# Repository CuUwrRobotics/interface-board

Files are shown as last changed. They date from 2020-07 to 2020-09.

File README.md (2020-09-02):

# Robot Hardware Interface Board

This repository contains [@nichlock](https://github.com/nichlock)'s design for our hardware interfacing board. This is the board which the [board-interface](https://github.com/CuUwrRobotics/PiranhaBot-docs/blob/master/board_interface/README.md) package is designed to control. 

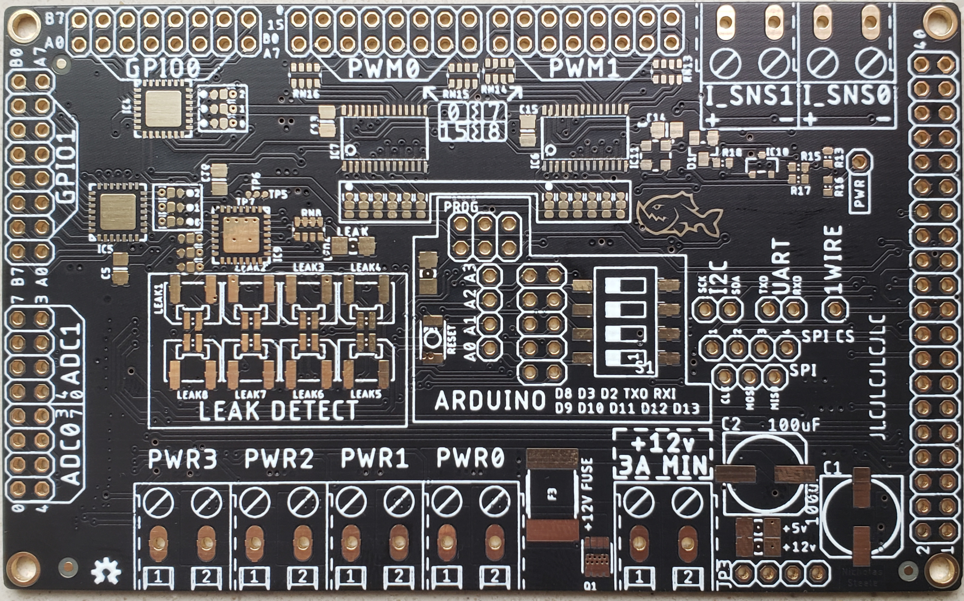
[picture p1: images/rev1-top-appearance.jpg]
Top of board, outside appearence


# Capabilities

This board is designed for our underwater robot, and connects to the Raspebrry Pi through the 40-pin header on the right. It has the following dedicated capabilities:
- 32 GPIO pins
- 32 PWM outputs
- 16 Analog inputs
- 8 Individual leak sensors
- 4 MOSFETs capable of driving 17A (connector limited)
- 2 Current sensors capable of 17A (connector limited, sensors are capable of 50A)
- 1 Microcontroller for I/O that needs constant attention
- 1 Configuration chooser, with 4 switches, for changing any setting on the fly

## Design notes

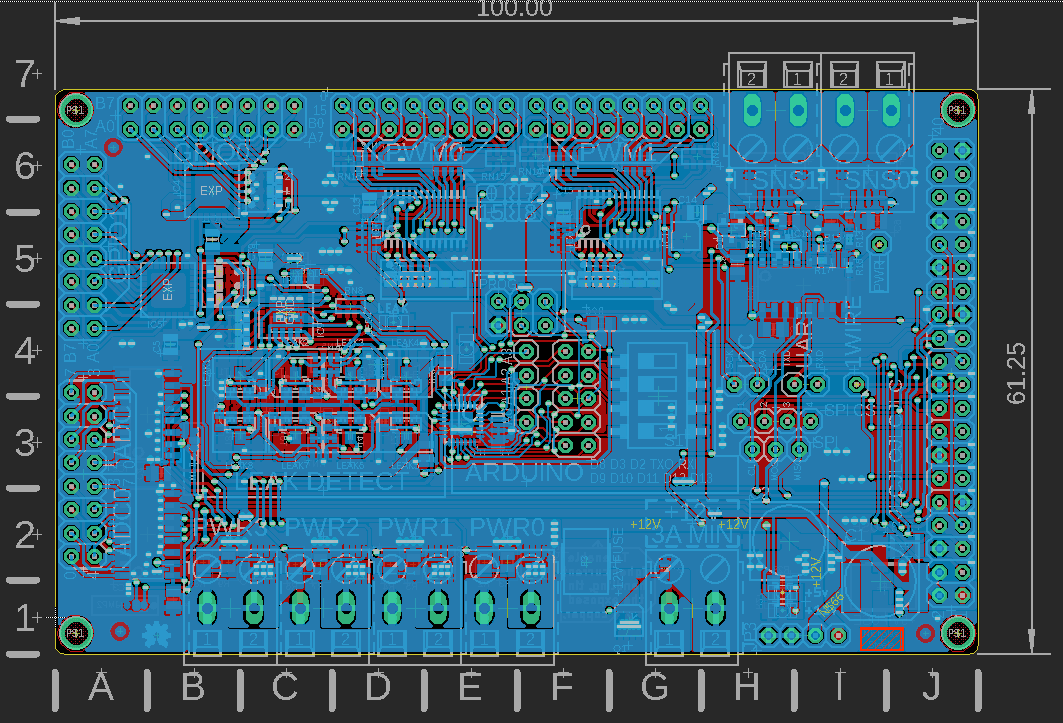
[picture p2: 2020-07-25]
images/rev1-bot-guts.png

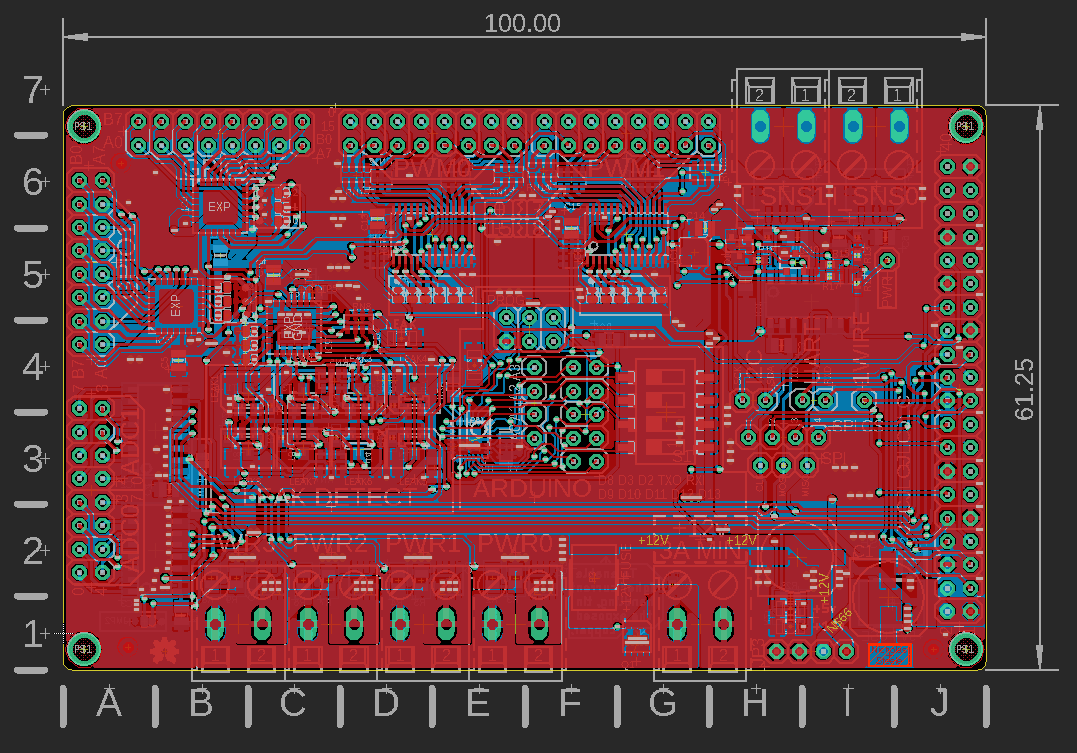
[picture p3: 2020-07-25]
images/rev1-top-guts.png

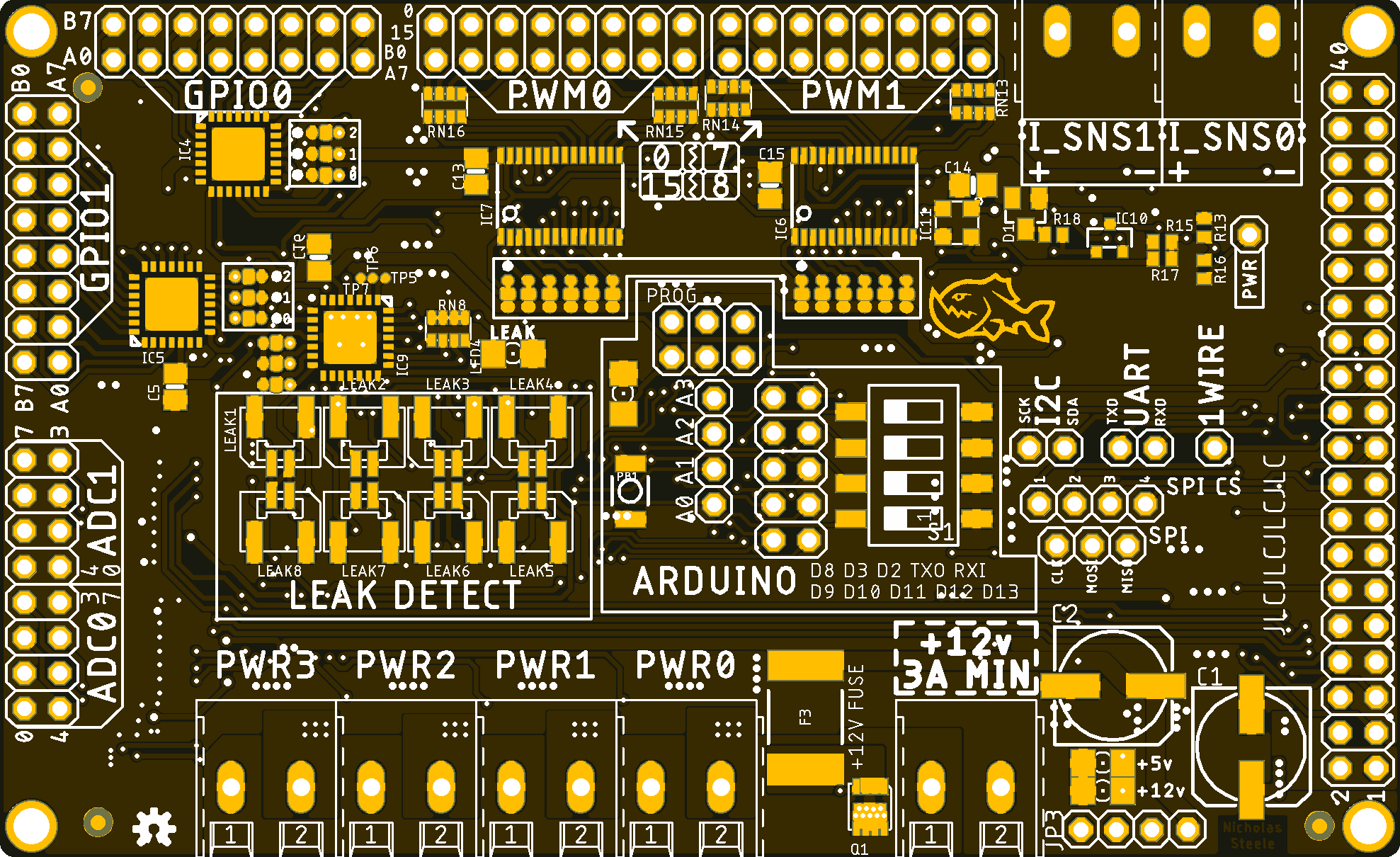
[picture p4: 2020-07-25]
images/rev1-top-appearance.png

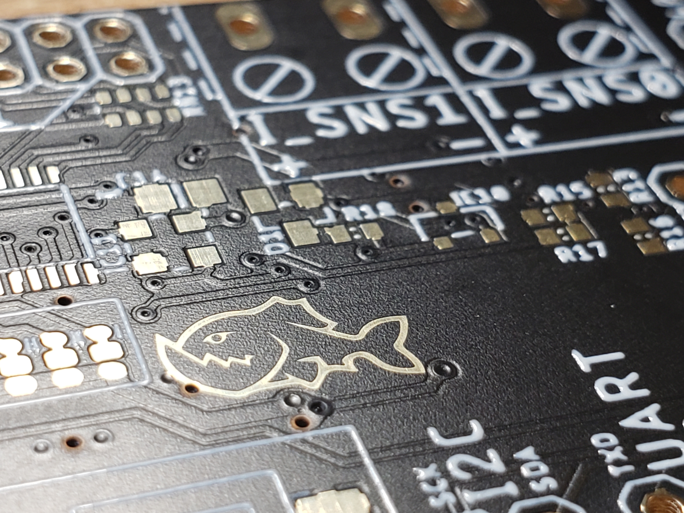
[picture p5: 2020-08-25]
images/piranha.jpg

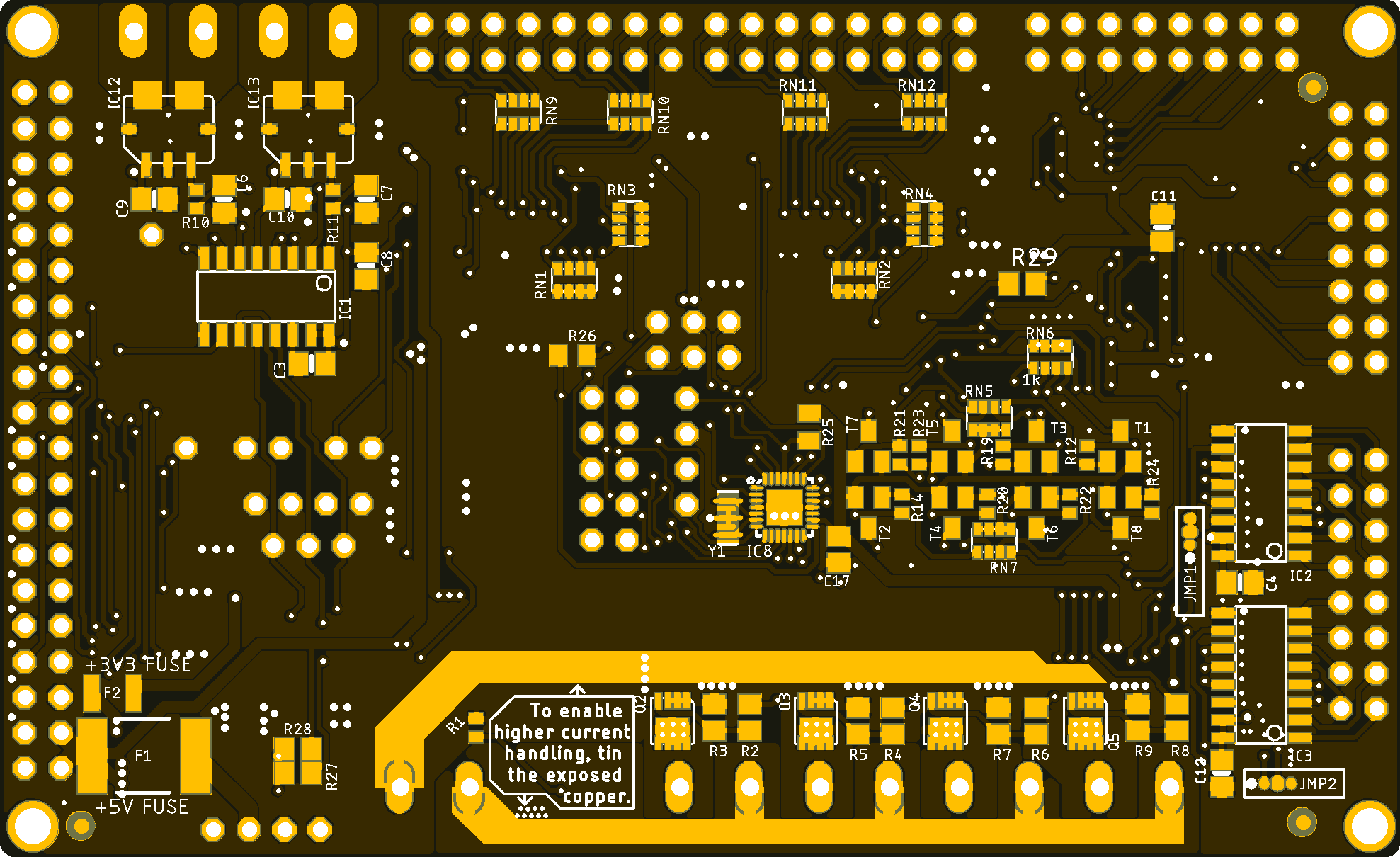
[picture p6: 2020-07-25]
images/rev1-bot-appearance.png

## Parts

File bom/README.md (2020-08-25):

# How to use this BOM

For purchasing, use `Circuit Board BOM.xlsx`. Enter the '1' for the functions you want included in the board on the table to the right, then copy the parts from the Auto Exporter page into Digikey/Mouser's BOM importer tools.

For an interactive BOM, use the files from the `interactive` directory in our web browser.

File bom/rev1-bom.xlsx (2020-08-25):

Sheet: Eagle Parts
100 | Value | Device | Package | Description | MFR ID | Mouser P/N | Digikey P/N | Cost | Count | Feature | Include? (1/0) | Cost Impact | Cost impact calc
C1 | 100uF | CPOL-US153CLV-0807 | 153CLV-0807 | Big 5v cap | PCV1J270MCL7GS | 647-PCV1J270MCL7GS |  | $2.82 | x | REQUIRED | x | 10.95 | $71.48
C2 | 100uF | CPOL-US153CLV-0807 | 153CLV-0807 | Big 12v cap | PCV1J270MCL7GS | 647-PCV1J270MCL7GS |  | $2.82 | x | Temp/pressure sensor | x | $3.87 | $31.28
C3 | 1uF | CAP_CERAMIC0805-NOOUTLINE | 0805-NO | ADC | CC0805ZRY5V7BB105 |  | 311-1457-1-ND | $0.16 | x | Current Sensors | 1 | $13.60 | $40.20
C4 | 1uF | CAP_CERAMIC0805-NOOUTLINE | 0805-NO | ADC | CC0805ZRY5V7BB105 |  | 311-1457-1-ND | $0.16 | x | Power switching | 1 | $10.08
C5 | 1uF | CAP_CERAMIC0805-NOOUTLINE | 0805-NO | ADC | CC0805ZRY5V7BB105 |  | 311-1457-1-ND | $0.16 | x | Arduino | x | $5.01
C6 | 1nF | CAP_CERAMIC0805-NOOUTLINE | 0805-NO | Current | CC0805JRX7R9BB102 |  | 311-4270-1-ND | $0.16 | 1 | Leak | 1 | $7.60
C7 | 1nF | CAP_CERAMIC0805-NOOUTLINE | 0805-NO | Current | CC0805JRX7R9BB103 |  | 311-4270-1-ND | $0.16 | 1 | ADC | x | $7.05
C8 | 1uF | CAP_CERAMIC0805-NOOUTLINE | 0805-NO | Temp | CC0805ZRY5V7BB105 |  | 311-1457-1-ND | $0.16 | x | GPIO | x | $3.40
C9 | .1uF | CAP_CERAMIC0805-NOOUTLINE | 0805-NO | Current | CC0805ZRY5V9BB104 |  | 311-1361-1-ND | $0.11 | 1 | PWM | x | $6.30
C10 | .1uF | CAP_CERAMIC0805-NOOUTLINE | 0805-NO | Current | CC0805ZRY5V9BB104 |  | 311-1361-1-ND | $0.11 | 1 | Parts for Security cam interface | 0 | $3.52
C11 | 10uF | CAP_CERAMIC0805-NOOUTLINE | 0805-NO | PWM | CC0805ZKY5V7BB106 | 603-CC805ZKY5V7BB106 |  | $0.29 | x | Already purchased items marked with x
C12 | 10uF | CAP_CERAMIC0805-NOOUTLINE | 0805-NO | PWM | CC0805ZKY5V7BB106 | 603-CC805ZKY5V7BB106 |  | $0.29 | x
C13 | 10uF | CAP_CERAMIC0805-NOOUTLINE | 0805-NO | GPIO | CC0805ZKY5V7BB106 | 603-CC805ZKY5V7BB106 |  | $0.29 | x
C14 | 1uF | CAP_CERAMIC0805-NOOUTLINE | 0805-NO | PRESS | CC0805ZRY5V7BB105 |  | 311-1457-1-ND | $0.16 | x
C15 | 10uF | CAP_CERAMIC0805-NOOUTLINE | 0805-NO | GPIO | CC0805ZKY5V7BB106 | 603-CC805ZKY5V7BB106 |  | $0.29 | x
C16 | 10uF | CAP_CERAMIC0805-NOOUTLINE | 0805-NO | Leak | CC0805ZKY5V7BB106 | 603-CC805ZKY5V7BB106 |  | $0.29 | 1
C17 | 0.1uF | C-EUC0805 | C0805 | Arduino | CC0805ZRY5V9BB104 |  | 311-1361-1-ND | $0.11 | x
D1 | BZX84B3V0-7-F | ZENER-DIODESOT23 | SOT23 | vref | BZX84B3V0-7-F | 621-BZX84B3V0-7-F |  | $0.17 | x
F1 | 3A | PTC_FUSE3 | 2920_(7351_METRIC) | 5v fuse | MF-LSMF300/24X-2 | 652-MF-LSMF300/24X-2 |  | $0.73 | x
F2 | 0.5A | PTC_FUSE2 | 1210_(3225METRIC) | 3v3 fuse | 0ZCH0050FF2G | 530-0ZCH0050FF2G |  | $0.11 | x
F3 | 3A | PTC_FUSE3 | 2920_(7351_METRIC) | 12v fuse | MF-LSMF300/24X-2 | 652-MF-LSMF300/24X-2 |  | $0.73 | x
IC1 | U2 | MCP3008 | MCP3008 | ADC | MCP3008-I/SL |  | MCP3008-I/SL-ND | $2.19 | x
IC2 | U2 | MCP3008 | MCP3008 | ADC | MCP3008-I/SL |  | MCP3008-I/SL-ND | $2.19 | x
IC3 | U2 | MCP3008 | MCP3008 | ADC | MCP3008-I/SL |  | MCP3008-I/SL-ND | $2.19 | x
IC4 | MCP23017ML | MCP23017ML | QFN28-ML_6X6MM | GPIO | MCP23017T-E/ML |  | MCP23017T-E/MLCT-ND | $1.41 | x
IC5 | MCP23017ML | MCP23017ML | QFN28-ML_6X6MM | GPIO | MCP23017T-E/ML |  | MCP23017T-E/MLCT-ND | $1.41 | x
IC6 | PCA9685 | PCA9685 | TSSOP28 | PWM | PCA9685PW/Q900,118 | 771-PCA9685PW,118 |  | $2.26 | x
IC7 | PCA9685 | PCA9685 | TSSOP28 | PWM | PCA9685PW/Q900,118 | 771-PCA9685PW,118 |  | $2.26 | x
IC8 | ATMEGA328P_VQFNVQFN | ATMEGA328P_VQFNVQFN | VQFN-28 | Arduino | ATMEGA328P-MMHR |  | ATMEGA328P-MMHRCT-ND | $2.17 | x
IC9 | MCP23017ML | MCP23017ML | QFN28-ML_6X6MM | Leak | MCP23017T-E/ML |  | MCP23017T-E/MLCT-ND | $1.41 | 1
IC10 | LM62C | LM62C | SOT23-R | Temp | LM62CIM3/NOPB |  | LM62CIM3/NOPBCT-ND | $1.13 | x
IC11 | MS563702BA03-50 | PRESSURE | MS5637 | PRESS | MS563702BA03-50 | 824-MS563702BA03-50 |  | $2.42 | x
IC12 | ACS780LLRTR-050B-T | ACS781 | ACS781 | Current, 100A | ACS780LLRTR-100U-T |  | 620-1820-1-ND | $5.27 | 1
IC13 | ACS780LLRTR-050B-T | ACS781 | ACS781 | Current, 50A | ACS780LLRTR-050U-T |  | 620-1818-1-ND | $5.27 | 1
LEAK1 | JST-GH-2 | JST-GH-2 | JST-GH | Leak | BM02B-GHS-TBT(LF)(SN)(N) |  | 455-1578-1-ND | $0.43 | 1
LEAK2 | JST-GH-2 | JST-GH-2 | JST-GH | Leak | BM02B-GHS-TBT(LF)(SN)(N) |  | 455-1578-1-ND | $0.43 | 1
LEAK3 | JST-GH-2 | JST-GH-2 | JST-GH | Leak | BM02B-GHS-TBT(LF)(SN)(N) |  | 455-1578-1-ND | $0.43 | 1
LEAK4 | JST-GH-2 | JST-GH-2 | JST-GH | Leak | BM02B-GHS-TBT(LF)(SN)(N) |  | 455-1578-1-ND | $0.43 | 1
LEAK5 | JST-GH-2 | JST-GH-2 | JST-GH | Leak | BM02B-GHS-TBT(LF)(SN)(N) |  | 455-1578-1-ND | $0.43 | 1
LEAK6 | JST-GH-2 | JST-GH-2 | JST-GH | Leak | BM02B-GHS-TBT(LF)(SN)(N) |  | 455-1578-1-ND | $0.43 | 1
LEAK7 | JST-GH-2 | JST-GH-2 | JST-GH | Leak | BM02B-GHS-TBT(LF)(SN)(N) |  | 455-1578-1-ND | $0.43 | 1
LEAK8 | JST-GH-2 | JST-GH-2 | JST-GH | Leak | BM02B-GHS-TBT(LF)(SN)(N) |  | 455-1578-1-ND | $0.43 | 1
LED1 |  | LED_E | LED_1206 | Arduino | LTST-C230KFKT | 859-LTST-C230KFKT |  | $0.30 | x
LED2 |  | LED_E | LED_1206 | 5v led | LTST-C230KFKT | 859-LTST-C230KFKT |  | $0.30 | x
LED3 |  | LED_E | LED_1206 | 12v led | LTST-C230KFKT | 859-LTST-C230KFKT |  | $0.30 | x
LED4 |  | LED_E | LED_1206 | Leak | LTST-C230KFKT | 859-LTST-C230KFKT |  | $0.30 | 1
PB1 | RESET | 0173_IT-1185AP1C-160G-G_T&R | SMD_157SW | Arduino | PTS820 J20M SMTR LFS |  | CKN10505CT-ND | $0.45 | x
Q1 | 1212_PFET | 1212_PFET | POWERPACK_1212-8 | reverse polarity | SI7625DN-T1-GE3 | 781-SI7625DN-T1-GE3 |  | $1.01 | x
Q2 | 1212_NFET | 1212_NFET | POWERPACK_1212-8 | pwr | SIS476DN-T1-GE3 |  | SIS476DN-T1-GE3CT-ND | $1.16 | 1
Q3 | 1212_NFET | 1212_NFET | POWERPACK_1212-8 | pwr | SIS476DN-T1-GE3 |  | SIS476DN-T1-GE3CT-ND | $1.16 | 1
Q4 | 1212_NFET | 1212_NFET | POWERPACK_1212-8 | pwr | SIS476DN-T1-GE3 |  | SIS476DN-T1-GE3CT-ND | $1.16 | 1
Q5 | 1212_NFET | 1212_NFET | POWERPACK_1212-8 | pwr | SIS476DN-T1-GE3 |  | SIS476DN-T1-GE3CT-ND | $1.16 | 1
R1 | 10k | R-US_R0402 | R0402 | reverse polarity | RC0805FR-0710KL |  | 311-10.0KCRCT-ND | $0.10 | x
R2 | 10R | R-US_R0805 | R0805 | pwr |  |  |  | $0.10 | 1
R3 | 10k | R-US_R0805 | R0805 | pwr | RC0805FR-0710KL |  | 311-10.0KCRCT-ND | $0.10 | 1
R4 | 10R | R-US_R0805 | R0805 | pwr |  |  |  | $0.10 | 1
R5 | 10k | R-US_R0805 | R0805 | pwr | RC0805FR-0710KL |  | 311-10.0KCRCT-ND | $0.10 | 1
R6 | 10R | R-US_R0805 | R0805 | pwr |  |  |  | $0.10 | 1
R7 | 10k | R-US_R0805 | R0805 | pwr | RC0805FR-0710KL |  | 311-10.0KCRCT-ND | $0.10 | 1
R8 | 10R | R-US_R0805 | R0805 | pwr |  |  |  | $0.10 | 1
R9 | 10k | R-US_R0805 | R0805 | pwr | RC0805FR-0710KL |  | 311-10.0KCRCT-ND | $0.10 | 1
R10 | 10k | R-US_R0402 | R0402 | Current | RC0805FR-0710KL |  | 311-10.0KCRCT-ND | $0.10 | 1
R11 | 10k | R-US_R0402 | R0402 | Current | RC0805FR-0710KL |  | 311-10.0KCRCT-ND | $0.10 | 1
R12 | 1k | R-US_R0402 | R0402 | Leak | RC0402FR-071KL |  | 311-1.00KLRCT-ND | $0.10 | 1
R13 | 1k | R-US_R0402 | R0402 | power line measure | RC0402FR-071KL |  | 311-1.00KLRCT-ND | $0.10 | x
R14 | 1k | R-US_R0402 | R0402 | Leak | RC0402FR-071KL |  | 311-1.00KLRCT-ND | $0.10 | 1
R15 | 1k | R-US_R0402 | R0402 | power line measure | RC0402FR-071KL |  | 311-1.00KLRCT-ND | $0.10 | x
R16 | 11k | R-US_R0402 | R0402 | power line measure | RC0402FR-0711KL |  | 311-11.0KLRCT-ND | $0.10 | x
R17 | 2.2k | R-US_R0402 | R0402 | power line measure | RC0402FR-072K2L |  | 311-2.20KLRCT-ND | $0.10 | x
R18 | 1k | R-US_R0402 | R0402 | vref | RC0402FR-071KL |  | 311-1.00KLRCT-ND | $0.10 | x
R19 | 1k | R-US_R0402 | R0402 | Leak | RC0402FR-071KL |  | 311-1.00KLRCT-ND | $0.10 | 1
R20 | 1k | R-US_R0402 | R0402 | Leak | RC0402FR-071KL |  | 311-1.00KLRCT-ND | $0.10 | 1
R21 | 1k | R-US_R0402 | R0402 | Leak | RC0402FR-071KL |  | 311-1.00KLRCT-ND | $0.10 | 1
R22 | 1k | R-US_R0402 | R0402 | Leak | RC0402FR-071KL |  | 311-1.00KLRCT-ND | $0.10 | 1
R23 | 1k | R-US_R0402 | R0402 | Leak | RC0402FR-071KL |  | 311-1.00KLRCT-ND | $0.10 | 1
R24 | 1k | R-US_R0402 | R0402 | Leak | RC0402FR-071KL |  | 311-1.00KLRCT-ND | $0.10 | 1
R25 | 10k | R-US_R0805 | R0805 | Arduino | RC0805FR-0710KL |  | 311-10.0KCRCT-ND | $0.10 | x
R26 | 1k | R-US_R0805 | R0805 | Arduino | RC0402FR-071KL |  | 311-1.00KLRCT-ND | $0.10 | x
R27 | 1k | R-US_R0805 | R0805 | 5v led | RC0402FR-071KL |  | 311-1.00KLRCT-ND | $0.10 | x
R28 | 1k | R-US_R0805 | R0805 | 12v led | RC0402FR-071KL |  | 311-1.00KLRCT-ND | $0.10 | x
R29 | 1k | R-US_R0805 | R0805 | Leak | RC0402FR-071KL |  | 311-1.00KLRCT-ND | $0.10 | x
RN1 | 10k | RN4_0804 | 0804_RN | PWM | CAY16-103J4LF |  | CAY16-103J4LFCT-ND | $0.10 | x
RN2 | 10k | RN4_0804 | 0804_RN | PWM | CAY16-103J4LF |  | CAY16-103J4LFCT-ND | $0.10 | x
RN3 | 10k | RN4_0804 | 0804_RN | PWM | CAY16-103J4LF |  | CAY16-103J4LFCT-ND | $0.10 | x
RN4 | 10k | RN4_0804 | 0804_RN | PWM | CAY16-103J4LF |  | CAY16-103J4LFCT-ND | $0.10 | x
RN5 | 27k | RN4_0804 | 0804_RN | Leak | CAY16-273J4LF | 652-CAY16-273J4LF |  | $0.10 | 1
RN6 | 1k | RN4_0804 | 0804_RN | Leak | CAY16-102J4LF |  | CAY16-102J4LFCT-ND | $0.10 | 1
RN7 | 27k | RN4_0804 | 0804_RN | Leak | CAY16-273J4LF | 652-CAY16-273J4LF |  | $0.10 | 1
RN8 | 1k | RN4_0804 | 0804_RN | Leak | CAY16-102J4LF |  | CAY16-102J4LFCT-ND | $0.10 | 1
RN9 | 220R | RN4_0804 | 0804_RN | PWM | CAY16-221J4LF |  | CAY16-221J4LFCT-ND | $0.10 | x
RN10 | 220R | RN4_0804 | 0804_RN | PWM | CAY16-221J4LF |  | CAY16-221J4LFCT-ND | $0.10 | x
RN11 | 220R | RN4_0804 | 0804_RN | PWM | CAY16-221J4LF |  | CAY16-221J4LFCT-ND | $0.10 | x
RN12 | 220R | RN4_0804 | 0804_RN | PWM | CAY16-221J4LF |  | CAY16-221J4LFCT-ND | $0.10 | x
RN13 | 220R | RN4_0804 | 0804_RN | PWM | CAY16-221J4LF |  | CAY16-221J4LFCT-ND | $0.10 | x
RN14 | 220R | RN4_0804 | 0804_RN | PWM | CAY16-221J4LF |  | CAY16-221J4LFCT-ND | $0.10 | x
RN15 | 220R | RN4_0804 | 0804_RN | PWM | CAY16-221J4LF |  | CAY16-221J4LFCT-ND | $0.10 | x
RN16 | 220R | RN4_0804 | 0804_RN | PWM | CAY16-221J4LF |  | CAY16-221J4LFCT-ND | $0.10 | x
S1 | SWS004 | SWS004 | SMS-004 | Arduino | A6S-4104-H | 653-A6S-4104-H |  | $1.49 | x
T1 | MMBT3906 | BC807-40-PNP-SOT23-BEC | SOT23-BEC | Leak | MMBT3906-7-F |  | MMBT3906-FDICT-ND | $0.12 | 1
T2 |  | BC807-40-PNP-SOT23-BEC | SOT23-BEC | Leak | MMBT3906-7-F |  | MMBT3906-FDICT-ND | $0.12 | 1
T3 |  | BC807-40-PNP-SOT23-BEC | SOT23-BEC | Leak | MMBT3906-7-F |  | MMBT3906-FDICT-ND | $0.12 | 1
T4 |  | BC807-40-PNP-SOT23-BEC | SOT23-BEC | Leak | MMBT3906-7-F |  | MMBT3906-FDICT-ND | $0.12 | 1
T5 |  | BC807-40-PNP-SOT23-BEC | SOT23-BEC | Leak | MMBT3906-7-F |  | MMBT3906-FDICT-ND | $0.12 | 1
T6 |  | BC807-40-PNP-SOT23-BEC | SOT23-BEC | Leak | MMBT3906-7-F |  | MMBT3906-FDICT-ND | $0.12 | 1
T7 |  | BC807-40-PNP-SOT23-BEC | SOT23-BEC | Leak | MMBT3906-7-F |  | MMBT3906-FDICT-ND | $0.12 | 1
T8 |  | BC807-40-PNP-SOT23-BEC | SOT23-BEC | Leak | MMBT3906-7-F |  | MMBT3906-FDICT-ND | $0.12 | 1
X1 |  | W237-102 | W237-102 | power input | 796689-2 | 571-796689-2 |  | $1.16 | x
X2 |  | W237-102 | W237-102 | pwr | 796689-2 | 571-796689-2 |  | $1.16 | 1
X3 |  | W237-102 | W237-102 | pwr | 796689-2 | 571-796689-2 |  | $1.16 | 1
X4 |  | W237-102 | W237-102 | pwr | 796689-2 | 571-796689-2 |  | $1.16 | 1
X5 |  | W237-102 | W237-102 | pwr | 796689-2 | 571-796689-2 |  | $1.16 | 1
X6 |  | W237-102 | W237-102 | Current | 796689-2 | 571-796689-2 |  | $1.16 | 1
X7 |  | W237-102 | W237-102 | Current | 796689-2 | 571-796689-2 |  | $1.16 | 1
Y1 | 8/16/20MHz | RESONATOR1:1 | RESONATOR-SMD-1:1 | Arduino | CSTNE16M0V530000R0 |  | 490-17948-1-ND | $0.29 | x
 |  |  |  | Cost without count: | $67.96 |  |  | $31.28 | 47
 |  |  |  | Security cam thing |  |  | MAX485CPA+-ND | 3.22 | 0
 |  |  |  | Security cam thing |  |  | 20QBK-ND | 0.1 | 0
 |  |  |  | Security cam thing |  |  | 20QBK-ND | 0.1 | 0
 |  |  |  | Security cam thing |  |  | 10KQBK-ND | 0.1 | 0
 |  |  |  |  | Total for sec. cam |  |  | 0
 |  |  |  | Cost without count: | $71.48 |  |  | $31.28

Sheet: Auto Exporter
Digikey P/N | Total QTY | Cost | Mouser P/N | Total QTY | Cost
0 | 0 | $0.00 | 647-PCV1J270MCL7GS | 0 | $5.64
311-1457-1-ND | 0 | $0.80 | 0 | 0 | $0.00
311-4270-1-ND | 2 | $0.32 | 603-CC805ZKY5V7BB106 | 1 | $1.45
311-1361-1-ND | 2 | $0.33 | 621-BZX84B3V0-7-F | 0 | $0.17
MCP3008-I/SL-ND | 0 | $6.57 | 652-MF-LSMF300/24X-2 | 0 | $1.46
MCP23017T-E/MLCT-ND | 1 | $4.23 | 530-0ZCH0050FF2G | 0 | $0.11
ATMEGA328P-MMHRCT-ND | 0 | $2.17 | 771-PCA9685PW,118 | 0 | $4.52
LM62CIM3/NOPBCT-ND | 0 | $1.13 | 824-MS563702BA03-50 | 0 | $2.42
620-1820-1-ND | 1 | $5.27 | 859-LTST-C230KFKT | 1 | $1.20
620-1818-1-ND | 1 | $5.27 | 781-SI7625DN-T1-GE3 | 0 | $1.01
455-1578-1-ND | 8 | $3.44 | 652-CAY16-273J4LF | 2 | $0.20
CKN10505CT-ND | 0 | $0.45 | 653-A6S-4104-H | 0 | $1.49
SIS476DN-T1-GE3CT-ND | 4 | $4.64 | 571-796689-2 | 6 | $8.12
311-10.0KCRCT-ND | 6 | $0.80 |  | 0 | $0.00
311-1.00KLRCT-ND | 8 | $1.50 |  | 0 | $0.00
311-11.0KLRCT-ND | 0 | $0.10 |  | 0 | $0.00
311-2.20KLRCT-ND | 0 | $0.10 |  | 0 | $0.00
CAY16-103J4LFCT-ND | 0 | $0.40 |  | 0 | $0.00
CAY16-102J4LFCT-ND | 2 | $0.20 |  | 0 | $0.00
CAY16-221J4LFCT-ND | 0 | $0.80 |  | 0 | $0.00
MMBT3906-FDICT-ND | 8 | $0.96 |  | 0 | $0.00
490-17948-1-ND | 0 | $0.29 |  | 0 | $0.00
MAX485CPA+-ND | 0 | $3.22 |  | 0 | $0.00
20QBK-ND | 0 | $0.20 |  | 0 | $0.00
10KQBK-ND | 0 | $0.10 |  | 0 | $0.00
 | 0 | $0.00 |  | 0 | $0.00
 | 0 | $0.00 |  | 0 | $0.00
 | 0 | $0.00 |  | 0 | $0.00
 | 0 | $0.00 |  | 0 | $0.00
 | 43 | $26.96 |  | 10 | $10.97
Overall total |  |  |  |  |  | $37.93

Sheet: Eagle Direct Export
Part | Value | Device | Package | Description | MFR ID | Mouser P/N | Digikey P/N | Cost | Notes | Count | Feature | Include? (1/0) | Cost impact | Cost impact calc | Options description | Cost @ 5 pcbs |  | Mouser | Digikey
C1 | 1uF | C-EUC0805 | C0805 | Ceramic Capacitors | CC0805ZRY5V7BB105 |  | 311-1457-1-ND | $0.16 |  | 1 | Temp sensor | 0 | $1.29 | 63.03 | DHL shipping (4 days) | $17.70 | Total | 18.67 | 19.78
C2 | 10uF | C-EUC0805 | C0805 | Ceramic Capacitors | CC0805ZKY5V7BB106 | 603-CC805ZKY5V7BB106 |  | $0.29 |  | 1 | Current Sensors | 0 | $13.60 | $35.48 | PostLink Shipping (20 days) | $5.34 | Shipping | 7.99 | 5.99
C3 | 100uF | CPOL-US153CLV-0807 | 153CLV-0807 | POLARIZED CAPACITOR, American symbol | PCV1J270MCL7GS | 647-PCV1J270MCL7GS |  | $2.82 | Main decoupling cap for 12v line | 1 | Pressure sesnor | 0 | $2.58 | $27.55
C4 | 10uF | C-EUC0805 | C0805 | Ceramic Capacitors | CC0805ZKY5V7BB106 | 603-CC805ZKY5V7BB106 |  | $0.29 |  | 1 | Power switching | 0 | $10.08 |  | Stencil cost | $7.00 | OVERALL TOTAL | $79.68
C5 | 1uF | C-EUC0805 | C0805 | Ceramic Capacitors | CC0805ZRY5V7BB105 |  | 311-1457-1-ND | $0.16 |  | 1 | Arduino | 1 | $4.82
C6 | 10uF | C-EUC0805 | C0805 | Ceramic Capacitors | CC0805ZKY5V7BB106 | 603-CC805ZKY5V7BB106 |  | $0.29 |  | 1 | OLED | 1 | $2.37 |  | Standard: green, leaded HASL | $2.00
C7 | 10uF | C-EUC0805 | C0805 | Ceramic Capacitors | CC0805ZKY5V7BB106 | 603-CC805ZKY5V7BB106 |  | $0.29 |  | 1 |  |  |  |  | Remove order number | $1.50
C7 | 10uF | C-EUC0805 | C0805 | Ceramic Capacitors | CC0805ZKY5V7BB106 | 603-CC805ZKY5V7BB106 |  | $0.29 |  | 1 |  |  |  |  | Black soldermask | $0.00
C8 | 1uF | C-EUC0805 | C0805 | Ceramic Capacitors | CC0805ZRY5V7BB105 |  | 311-1457-1-ND | $0.16 |  | 1 |  |  |  |  | Lead-free HASL | $5.30
C9 | 1uF | C-EUC0805 | C0805 | Ceramic Capacitors | CC0805ZRY5V7BB105 |  | 311-1457-1-ND | $0.16 |  | 1 |  |  |  |  | ENIG plating | $16.00
C10 | 1uF | C-EUC0805 | C0805 | Ceramic Capacitors | CC0805ZRY5V7BB105 |  | 311-1457-1-ND | $0.16 |  | 1
C11 | 1uF | C-EUC0805 | C0805 | Ceramic Capacitors | CC0805ZRY5V7BB105 |  | 311-1457-1-ND | $0.16 |  | 1
C12 | 10uF | C-EUC0805 | C0805 | Ceramic Capacitors | CC0805ZKY5V7BB106 | 603-CC805ZKY5V7BB106 |  | $0.29 |  | 1
C13 | 2.2uF | C-EUC0805 | C0805 | Ceramic Capacitors | CC0805ZRY5V7BB225 |  | 311-1463-1-ND | $0.19 |  | 1
C14 | 1uF | C-EUC0805 | C0805 | Ceramic Capacitors | CC0805ZRY5V7BB105 |  | 311-1457-1-ND | $0.16 |  | 0
C15 | .1uF | C-EUC0805 | C0805 | Ceramic Capacitors | CC0805ZRY5V9BB104 |  | 311-1361-1-ND | $0.11 |  | 0
C16 | 1uF | C-EUC0805 | C0805 | Ceramic Capacitors | CC0805ZRY5V7BB105 |  | 311-1457-1-ND | $0.16 |  | 0
C17 | .1uF | C-EUC0805 | C0805 | Ceramic Capacitors | CC0805ZRY5V9BB104 |  | 311-1361-1-ND | $0.11 |  | 0
C18 | 1uF | C-EUC0805 | C0805 | Ceramic Capacitors | CC0805ZRY5V7BB105 |  | 311-1457-1-ND | $0.16 |  | 1
C19 | 1uF | C-EUC0805 | C0805 | Ceramic Capacitors | CC0805ZRY5V7BB105 |  | 311-1457-1-ND | $0.16 |  | 0
C20 | 1uF | C-EUC0805 | C0805 | Ceramic Capacitors | CC0805ZRY5V7BB105 |  | 311-1457-1-ND | $0.16 |  | 0
C22 | 100uF | CPOL-US153CLV-0807 | 153CLV-0807 | POLARIZED CAPACITOR, American symbol | PCV1J270MCL7GS | 647-PCV1J270MCL7GS |  | $2.82 | Main decoupling cap for 5v line | 1
C23 | 0.1uF | C-EUC0805 | C0805 | Ceramic Capacitors | CC0805ZRY5V9BB104 |  | 311-1361-1-ND | $0.11 |  | 1
C24 | 0.1uF | C-EUC0805 | C0805 | Ceramic Capacitors | CC0805ZRY5V9BB104 |  | 311-1361-1-ND | $0.11 |  | 1
D1 | 1N4148 | DIODESOD-323 | SOD-323 | Diode | 1N4148WS-7-F |  | 1N4148WS-FDICT-ND | $0.17 |  | 1
D2 | BZX84B3V0-7-F | ZENER-DIODESOT23 | SOT23 | Z-Diode | BZX84B3V0-7-F | 621-BZX84B3V0-7-F |  | $0.17 |  | 1
F1 | 3A | PTC_FUSE3 | 2920_(7351_METRIC) |  | MF-LSMF300/24X-2 | 652-MF-LSMF300/24X-2 |  | $0.73 | 12V fuse | 1
F2 | 3A | PTC_FUSE | 2920_(7351_METRIC) | Bel Fuse Inc. | MF-LSMF300/24X-2 | 652-MF-LSMF300/24X-2 |  | $0.73 | 5V fuse | 1
F3 | .5A | PTC_FUSE | 1210_(3225METRIC) | Bel Fuse Inc. | 0ZCH0050FF2G | 530-0ZCH0050FF2G |  | $0.11 | 3V3 fuse | 1
IC1 | MCP23017ML | MCP23017ML | QFN28-ML_6X6MM |  | MCP23017T-E/ML |  | MCP23017T-E/MLCT-ND | $1.41 | GPIO Expander | 1
IC2 | MCP23017ML | MCP23017ML | QFN28-ML_6X6MM |  | MCP23017T-E/ML |  | MCP23017T-E/MLCT-ND | $1.41 | GPIO Expander | 1
IC3 | U2 | MCP3008 | MCP3008 |  | MCP3008-I/SL |  | MCP3008-I/SL-ND | $2.19 | ADC | 1
IC4 | U2 | MCP3008 | MCP3008 |  | MCP3008-I/SL |  | MCP3008-I/SL-ND | $2.19 | ADC | 1
IC5 | U2 | MCP3008 | MCP3008 |  | MCP3008-I/SL |  | MCP3008-I/SL-ND | $2.19 | ADC | 1
IC7 | PCA9685 | PCA9685 | TSSOP28 | PCA9685 - 16 Channel 12-Bit I2C PWM Controller | PCA9685PW/Q900,118 | 771-PCA9685PW,118 |  | $2.26 | PWM Driver | 1
IC8 | PCA9685 | PCA9685 | TSSOP28 | PCA9685 - 16 Channel 12-Bit I2C PWM Controller | PCA9685PW/Q900,118 | 771-PCA9685PW,118 |  | $2.26 | PWM Driver | 1
IC9 | MS563702BA03-50 | PRESSURE | MS5637 | Pressure Sensor | MS563702BA03-50 | 824-MS563702BA03-50 |  | $2.42 | Ambient Pressure | 0
IC10 | ACS780LLRTR-050B-T | ACS781 | ACS781 |  | ACS780LLRTR-050B-T |  | 620-1817-1-ND | $5.27 | Current sensor | 0
IC11 | ACS780LLRTR-050B-T | ACS781 | ACS781 |  | ACS780LLRTR-050B-T |  | 620-1817-1-ND | $5.27 | Current sensor | 0
IC12 | LM62C | LM62C | SOT23-R | TI's Thermal Sensor LM62CIM3/NOPB | LM62CIM3/NOPB |  | 926-LM62CIM3/NOPB | $1.13 | Ambient temp sensor | 0
IC13 | ATMEGA328P_VQFNVQFN | ATMEGA328P_VQFNVQFN | VQFN-28 | Atmel 328P | ATMEGA328P-MMHR |  | ATMEGA328P-MMHRCT-ND | $2.17 | Arduino chip | 1
LED1 |  | LED_E | LED_1206 | LED | LTST-C230KFKT | 859-LTST-C230KFKT |  | $0.30 |  | 1
LED2 |  | LED_E | LED_1206 | LED | LTST-C230KFKT | 859-LTST-C230KFKT |  | $0.30 |  | 1
LED3 |  | LED_E | LED_1206 | LED | LTST-C230KFKT | 859-LTST-C230KFKT |  | $0.30 |  | 1
Q1 | 1212_PFET | 1212_PFET | POWERPACK_1212-8 | Vishay Siliconix | SI7625DN-T1-GE3 | 781-SI7625DN-T1-GE3 |  | $1.01 | Reverse voltage protection | 1
Q2 | 1212_NFET | 1212_NFET | POWERPACK_1212-8 | Vishay Siliconix | SIS476DN-T1-GE3 |  | SIS476DN-T1-GE3CT-ND | $1.16 | PWR control fet | 0
Q3 | 1212_NFET | 1212_NFET | POWERPACK_1212-8 | Vishay Siliconix | SIS476DN-T1-GE3 |  | SIS476DN-T1-GE3CT-ND | $1.16 | PWR control fet | 0
Q4 | 1212_NFET | 1212_NFET | POWERPACK_1212-8 | Vishay Siliconix | SIS476DN-T1-GE3 |  | SIS476DN-T1-GE3CT-ND | $1.16 | PWR control fet | 0
Q5 | 1212_NFET | 1212_NFET | POWERPACK_1212-8 | Vishay Siliconix | SIS476DN-T1-GE3 |  | SIS476DN-T1-GE3CT-ND | $1.16 | PWR control fet | 0
Q6 | BSS138 | MOSFET-NWIDE | SOT23-WIDE | N-Channel Mosfet | BSS138 | 621-BSS138-13-F |  | $0.24 |  | 1
Q7 | BSS138 | MOSFET-NWIDE | SOT23-WIDE | N-Channel Mosfet | BSS138 | 621-BSS138-13-F |  | $0.24 |  | 1
Q8 | 8/16/20MHz | RESONATOR1:1 | RESONATOR-SMD-1:1 | Resonator | CSTNE16M0V530000R0 |  | 490-17948-1-ND | $0.29 |  | 1
R1 | 10k | R-US_R0805 | R0805 | RESISTOR, American symbol | RC0805FR-0710KL |  | 311-10.0KCRCT-ND | $0.10 |  | 0
R2 | 10k | R-US_R0805 | R0805 | RESISTOR, American symbol | RC0805FR-0710KL |  | 311-10.0KCRCT-ND | $0.10 |  | 0
R3 | 1k | R-US_R0805 | R0805 | RESISTOR, American symbol | RC0805JR-07470RL |  | 311-470ARCT-ND | $0.10 |  | 1
R5 | 1k | R-US_R0805 | R0805 | RESISTOR, American symbol | RC0805JR-07470RL |  | 311-470ARCT-ND | $0.10 |  | 1
R6 | 10k | R-US_R0805 | R0805 | RESISTOR, American symbol | RC0805FR-0710KL |  | 311-10.0KCRCT-ND | $0.10 |  | 0
R7 | 10k | R-US_R0805 | R0805 | RESISTOR, American symbol | RC0805FR-0710KL |  | 311-10.0KCRCT-ND | $0.10 |  | 0
R8 | 10k | R-US_R0805 | R0805 | RESISTOR, American symbol | RC0805FR-0710KL |  | 311-10.0KCRCT-ND | $0.10 |  | 0
R9 | 10k | R-US_R0805 | R0805 | RESISTOR, American symbol | RC0805FR-0710KL |  | 311-10.0KCRCT-ND | $0.10 |  | 0
R10 | 10k | R-US_R0805 | R0805 | RESISTOR, American symbol | RC0805FR-0710KL |  | 311-10.0KCRCT-ND | $0.10 |  | 0
R11 | 10k | R-US_R0805 | R0805 | RESISTOR, American symbol | RC0805FR-0710KL |  | 311-10.0KCRCT-ND | $0.10 |  | 0
R12 | 10k | R-US_R0805 | R0805 | Resistors | RC0805FR-0710KL |  | 311-10.0KCRCT-ND | $0.10 |  | 1
R13 | 10k | R-US_R0402 | R0402 | RESISTOR, American symbol | RC0402FR-0710KL |  | 311-10.0KLRCT-ND | $0.10 | Reverse voltage prot circuit | 1
R14 | 10k | RESISTOR0805 | R0805 | Resistors | RC0805FR-0710KL |  | 311-10.0KCRCT-ND | $0.10 |  | 1
R15 | 10k | RESISTOR0805 | R0805 | Resistors | RC0805FR-0710KL |  | 311-10.0KCRCT-ND | $0.10 |  | 1
R16 | 10k | RESISTOR0805 | R0805 | Resistors | RC0805FR-0710KL |  | 311-10.0KCRCT-ND | $0.10 |  | 1
R17 | 10k | RESISTOR0805 | R0805 | Resistors | RC0805FR-0710KL |  | 311-10.0KCRCT-ND | $0.10 |  | 1
R18 | 390k | RESISTOR0805 | R0805 | Resistors | RC0805FR-07390KL |  | 311-390KCRCT-ND | $0.10 |  | 1
R19 | 10k | R-US_R0402 | R0402 | RESISTOR, American symbol | RC0402FR-0710KL |  | 311-10.0KLRCT-ND | $0.10 | Current sensor | 0
R20 | 10k | R-US_R0402 | R0402 | RESISTOR, American symbol | RC0402FR-0710KL |  | 311-10.0KLRCT-ND | $0.10 | Current sensor | 0
R21 | 1k | R-US_R0402 | R0402 | RESISTOR, American symbol | RC0402FR-071KL |  | 311-1.00KLRCT-ND | $0.10 |  | 1
R22 | 11k | R-US_R0402 | R0402 | RESISTOR, American symbol | RC0402FR-0711KL |  | 311-11.0KLRCT-ND | $0.10 |  | 1
R23 | 2.2k | R-US_R0402 | R0402 | RESISTOR, American symbol | RC0402FR-072K2L |  | 311-2.20KLRCT-ND | $0.10 |  | 1
R24 | 1k | R-US_R0402 | R0402 | RESISTOR, American symbol | RC0402FR-071KL |  | 311-1.00KLRCT-ND | $0.10 |  | 1
R25 | 1k | R-US_R0402 | R0402 | RESISTOR, American symbol | RC0402FR-071KL |  | 311-1.00KLRCT-ND | $0.10 |  | 1
R26 | 10K | R-US_R0805 | R0805 | RESISTOR, American symbol | RC0402FR-0710KL |  | 311-10.0KLRCT-ND | $0.10 |  | 1
R27 | 1k | R-US_R0805 | R0805 | RESISTOR, American symbol | RC0402FR-071KL |  | 311-1.00KLRCT-ND | $0.10 |  | 1
RN1 | 10k | RN4_0804 | 0804_RN |  | CAY16-103J4LF |  | CAY16-103J4LFCT-ND | $0.10 |  | 0
RN3 | 220R | RN4_0804 | 0804_RN | Chip Resistor Array 4 Single Resistor | CAY16-221J4LF |  | CAY16-221J4LFCT-ND | $0.10 |  | 1
RN4 | 220R | RN4_0804 | 0804_RN | Chip Resistor Array 4 Single Resistor | CAY16-221J4LF |  | CAY16-221J4LFCT-ND | $0.10 |  | 1
RN5 | 220R | RN4_0804 | 0804_RN | Chip Resistor Array 4 Single Resistor | CAY16-221J4LF |  | CAY16-221J4LFCT-ND | $0.10 |  | 1
RN6 | 220R | RN4_0804 | 0804_RN | Chip Resistor Array 4 Single Resistor | CAY16-221J4LF |  | CAY16-221J4LFCT-ND | $0.10 |  | 1
RN7 | 220R | RN4_0804 | 0804_RN | Chip Resistor Array 4 Single Resistor | CAY16-221J4LF |  | CAY16-221J4LFCT-ND | $0.10 |  | 1
RN8 | 220R | RN4_0804 | 0804_RN | Chip Resistor Array 4 Single Resistor | CAY16-221J4LF |  | CAY16-221J4LFCT-ND | $0.10 |  | 1
RN9 | 220R | RN4_0804 | 0804_RN | Chip Resistor Array 4 Single Resistor | CAY16-221J4LF |  | CAY16-221J4LFCT-ND | $0.10 |  | 1
RN10 | 220R | RN4_0804 | 0804_RN | Chip Resistor Array 4 Single Resistor | CAY16-221J4LF |  | CAY16-221J4LFCT-ND | $0.10 |  | 1
RN11 | 10k | RN4_0804 | 0804_RN | Chip Resistor Array 4 Single Resistor | CAY16-103J4LF |  | CAY16-103J4LFCT-ND | $0.10 |  | 1
RN12 | 10k | RN4_0804 | 0804_RN | Chip Resistor Array 4 Single Resistor | CAY16-103J4LF |  | CAY16-103J4LFCT-ND | $0.10 |  | 1
RN13 | 10k | RN4_0804 | 0804_RN | Chip Resistor Array 4 Single Resistor | CAY16-103J4LF |  | CAY16-103J4LFCT-ND | $0.10 |  | 1
RN14 | 10k | RN4_0804 | 0804_RN | Chip Resistor Array 4 Single Resistor | CAY16-103J4LF |  | CAY16-103J4LFCT-ND | $0.10 |  | 1
S1 | SWS004 | SWS004 | SMS-004 | SMD Dip Switch 4 pol. | A6S-4104-H | SW1011-ND |  | $1.49 |  | 1
S2 | RESET | 0173_IT-1185AP1C-160G-G_T&R | SMD_157SW | Pushbutton 4x3 SMD H2,5mm | PTS820 J20M SMTR LFS |  | CKN10505CT-ND | $0.45 | Adru reset | 1
X1 |  | W237-102 | W237-102 | WAGO SCREW CLAMP | 796689-2 | 571-796689-2 |  | $1.16 | Main power connector | 1
X2 |  | W237-102 | W237-102 | WAGO SCREW CLAMP | 796689-2 | 571-796689-2 |  | $1.16 |  | 0
X3 |  | W237-102 | W237-102 | WAGO SCREW CLAMP | 796689-2 | 571-796689-2 |  | $1.16 |  | 0
X4 |  | W237-102 | W237-102 | WAGO SCREW CLAMP | 796689-2 | 571-796689-2 |  | $1.16 |  | 0
X5 |  | W237-102 | W237-102 | WAGO SCREW CLAMP | 796689-2 | 571-796689-2 |  | $1.16 |  | 0
X6 |  | W237-102 | W237-102 | WAGO SCREW CLAMP | 796689-2 | 571-796689-2 |  | $1.16 | Current sensor | 0
X7 |  | W237-102 | W237-102 | WAGO SCREW CLAMP | 796689-2 | 571-796689-2 |  | $1.16 | Current sensor | 0
Total |  |  |  |  |  |  |  | $35.48 |  | 69
security interface |  |  |  | MAX485 | MAX485CPA+ |  | MAX485CPA+-ND | 3.22 |  | 1
 | 20R |  |  | Resistors | CFR-25JB-52-20R |  | 20QBK-ND | 0.1 |  | 1
 |  |  |  |  | CFR-25JB-52-20R |  | 20QBK-ND | 0.1 |  | 1
 | 10K |  |  |  | CFR-25JB-52-10K |  | 10KQBK-ND | 0.1 |  | 1
 |  |  |  |  |  |  |  | $39.00

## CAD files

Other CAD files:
eagle/rev1-bcream.dxf
eagle/rev1-tcream.dxf

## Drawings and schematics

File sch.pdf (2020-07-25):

# ADC/ANALOG SENSORS

# POWER LINE MEASUREMENT

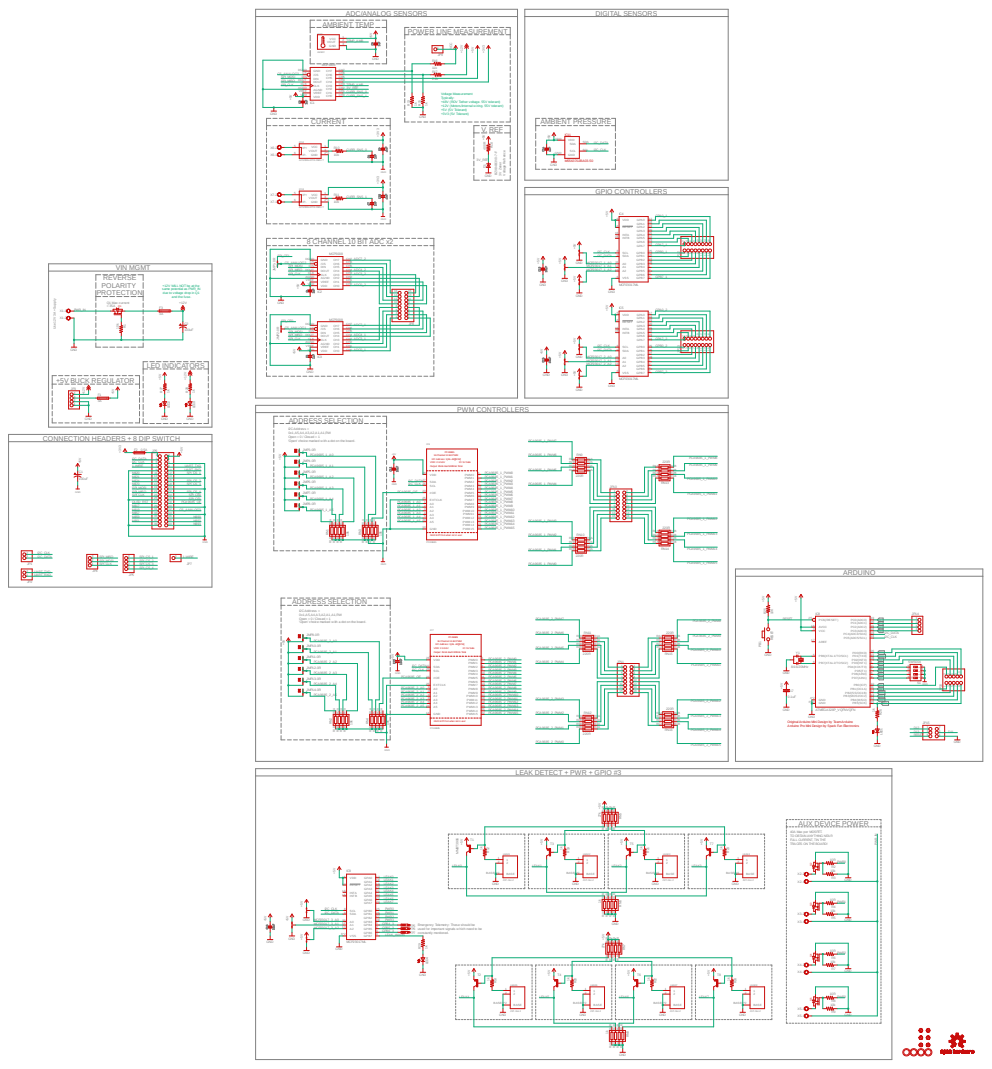
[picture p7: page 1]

V. REF AMBIENT TEMP CURRENT

ADDRESS SELECTION Use 12V ³A⁺ Supply

CONNECTION HEADERS + 8 DIP SWITCH
100uF ⁺⁵V GND

FULL CURRENT, TIN THE TRACES ON THE BOARD!

Emergency Telemetry: These should be

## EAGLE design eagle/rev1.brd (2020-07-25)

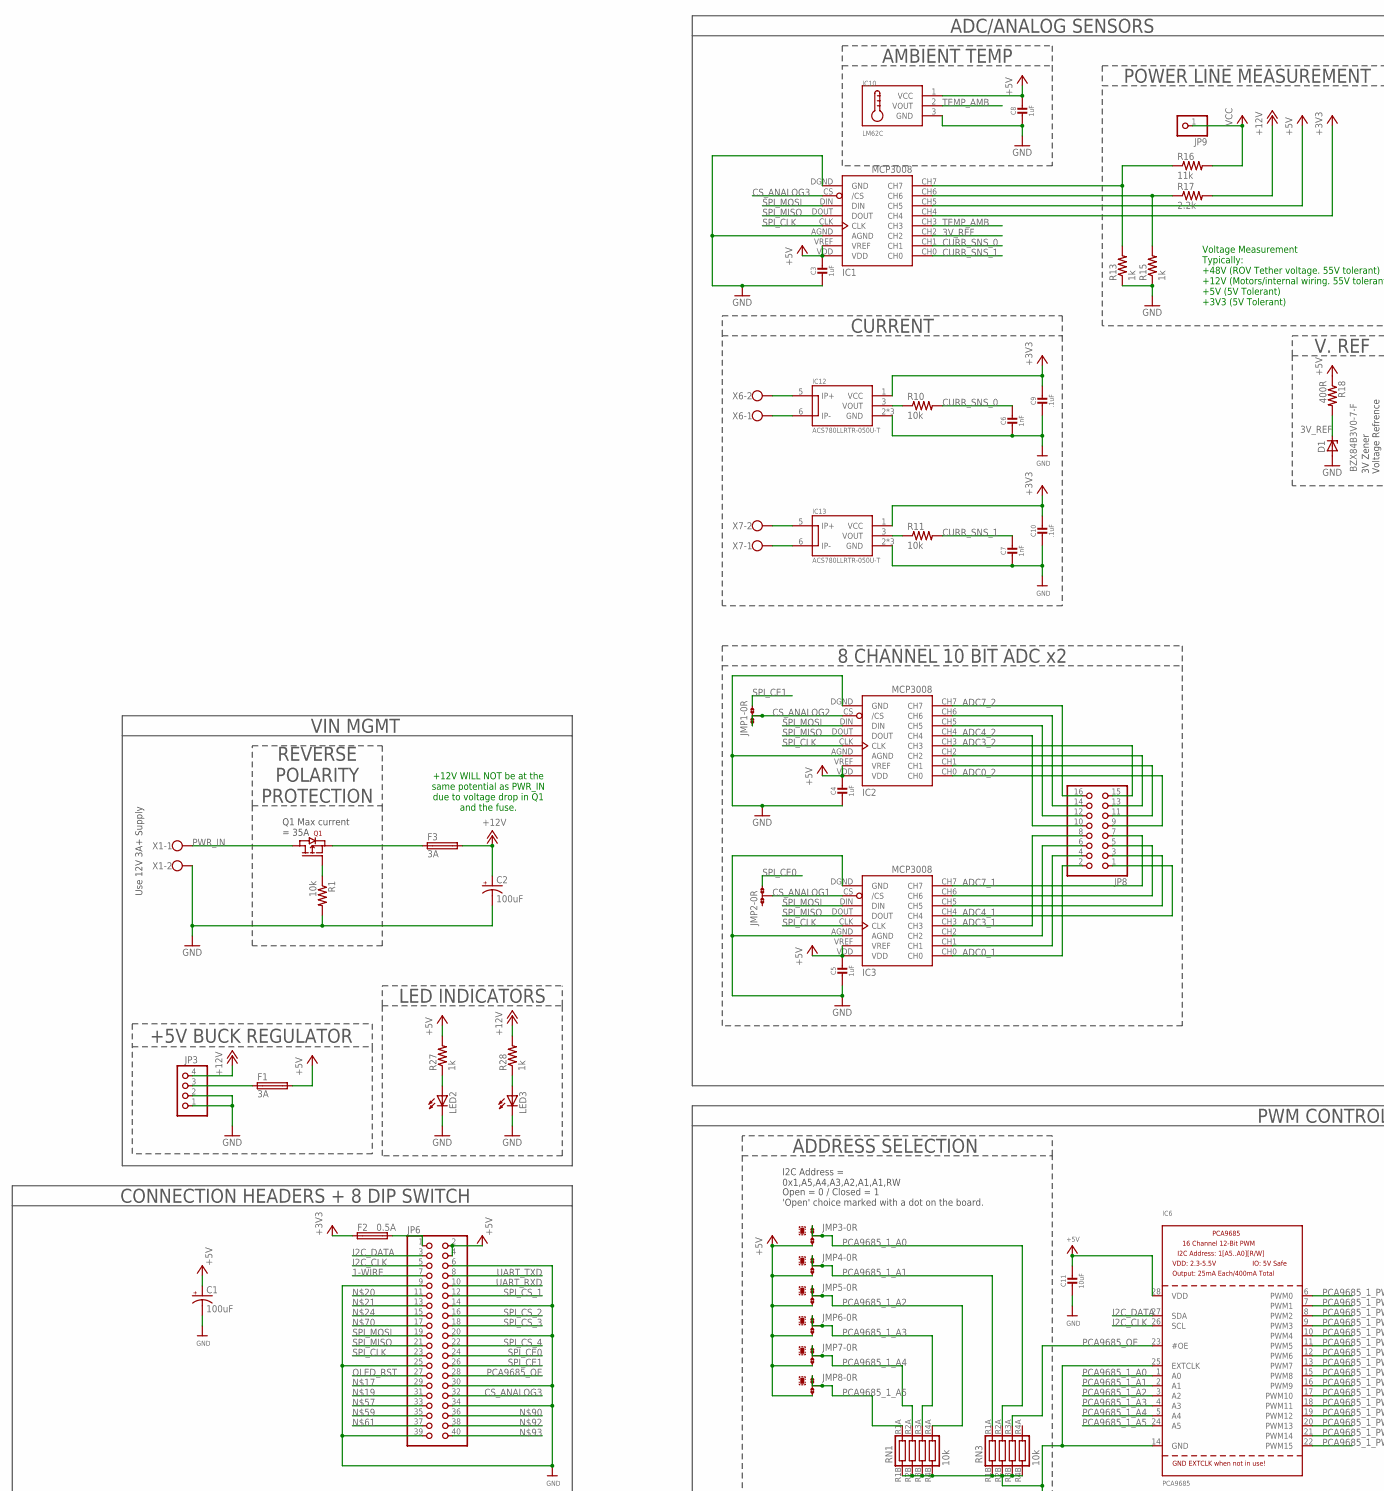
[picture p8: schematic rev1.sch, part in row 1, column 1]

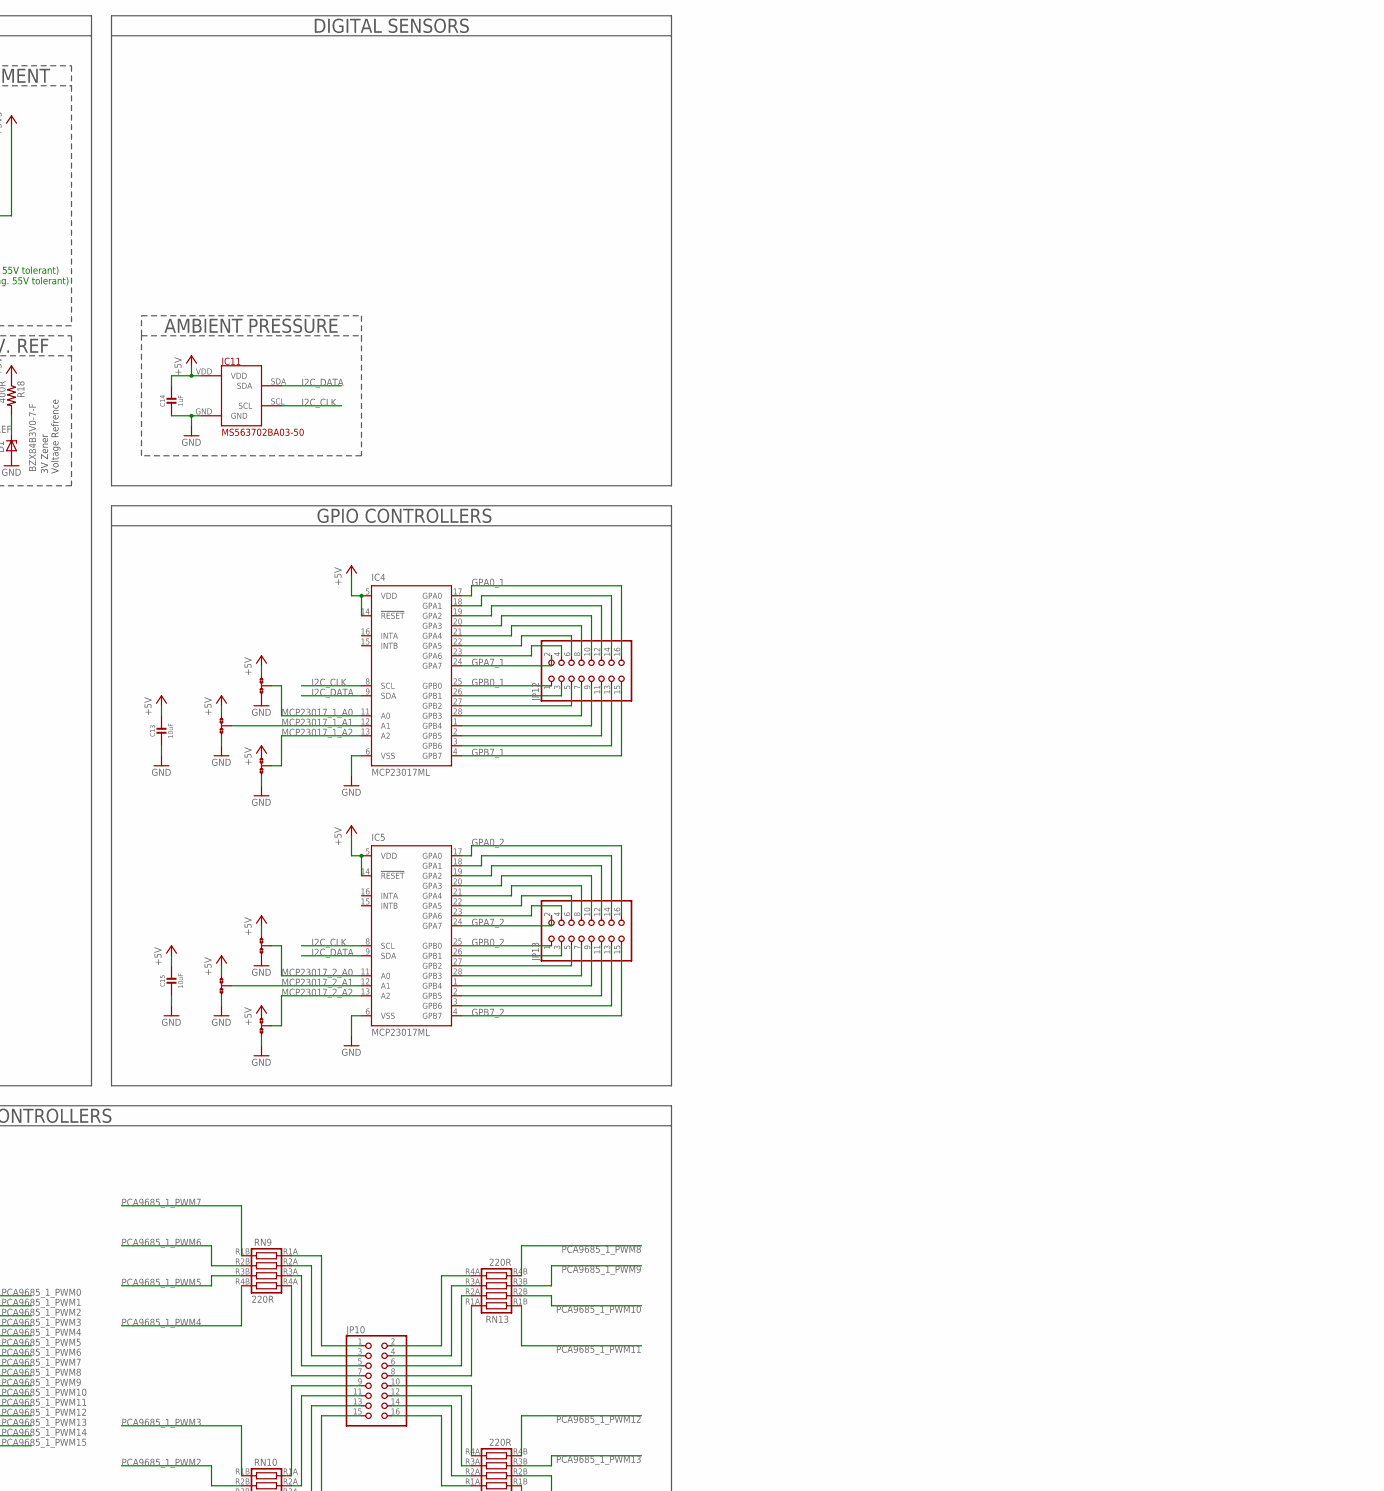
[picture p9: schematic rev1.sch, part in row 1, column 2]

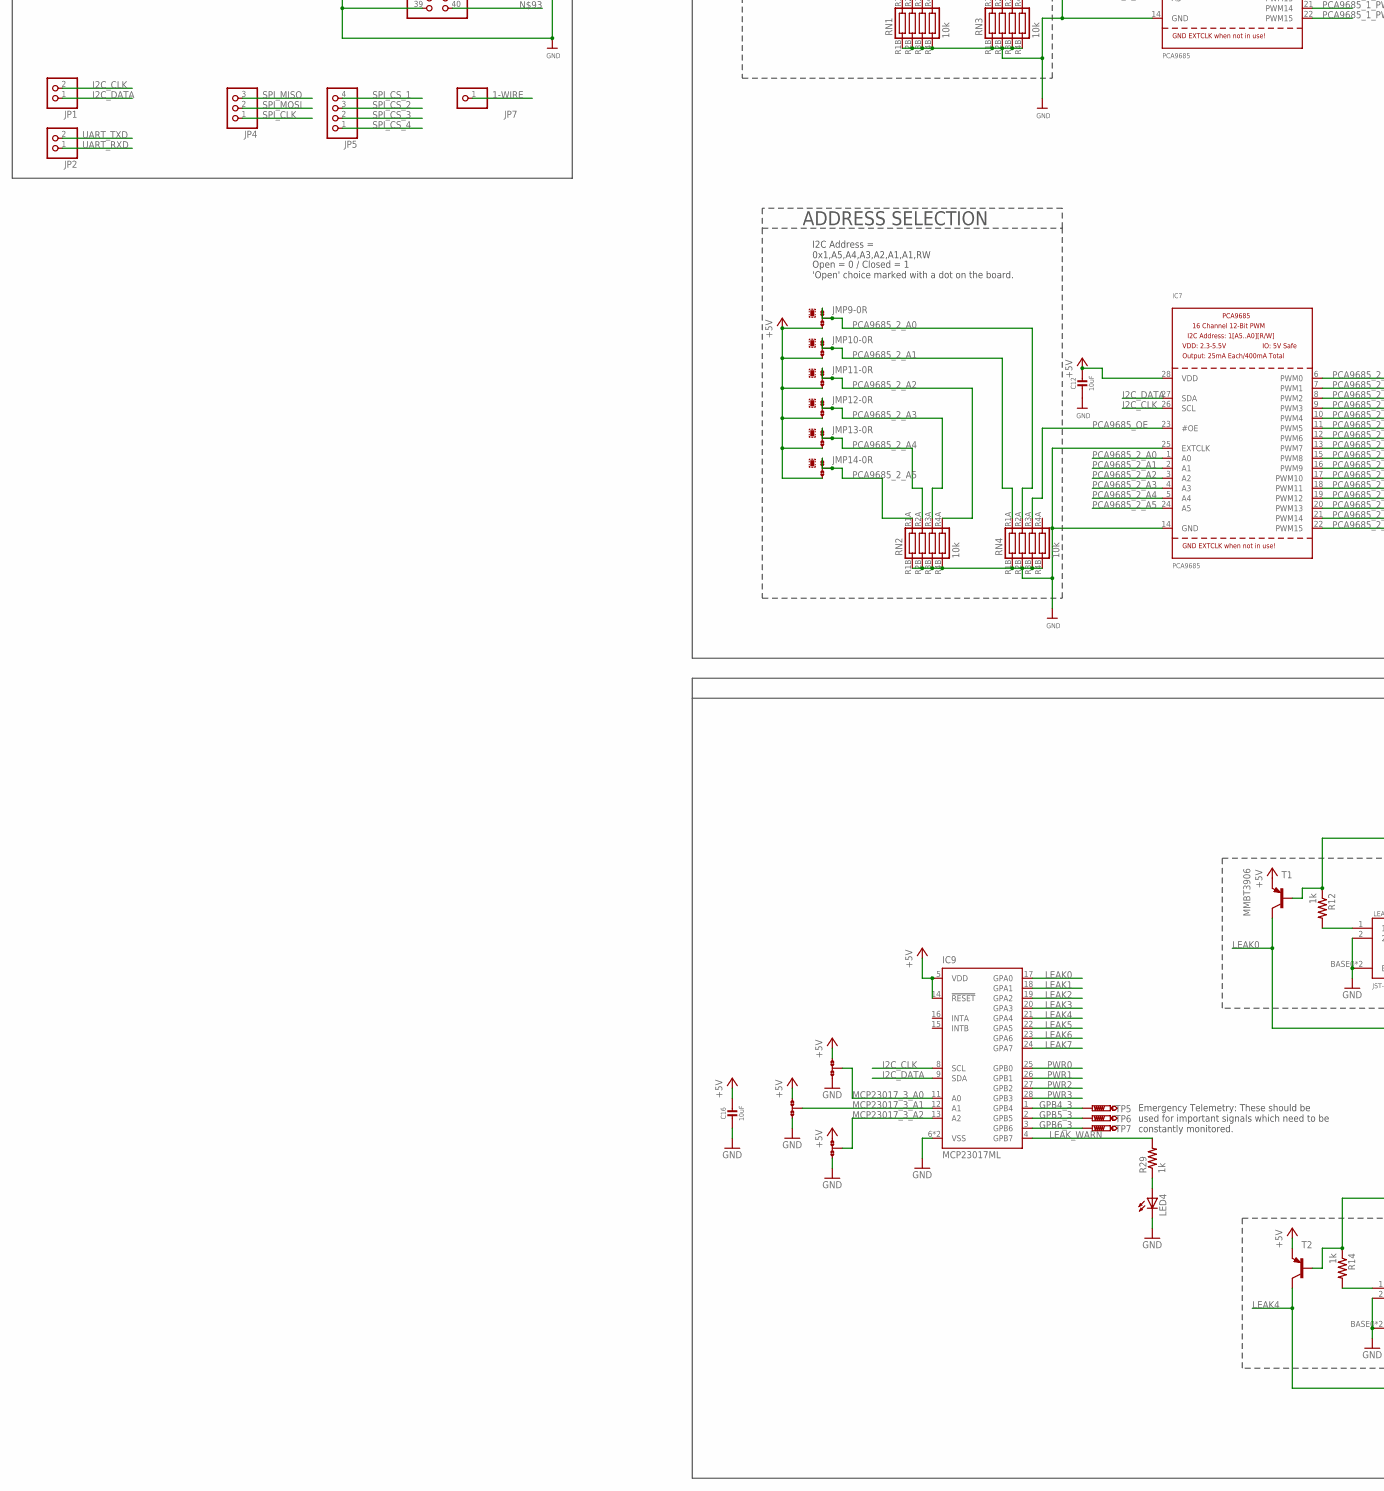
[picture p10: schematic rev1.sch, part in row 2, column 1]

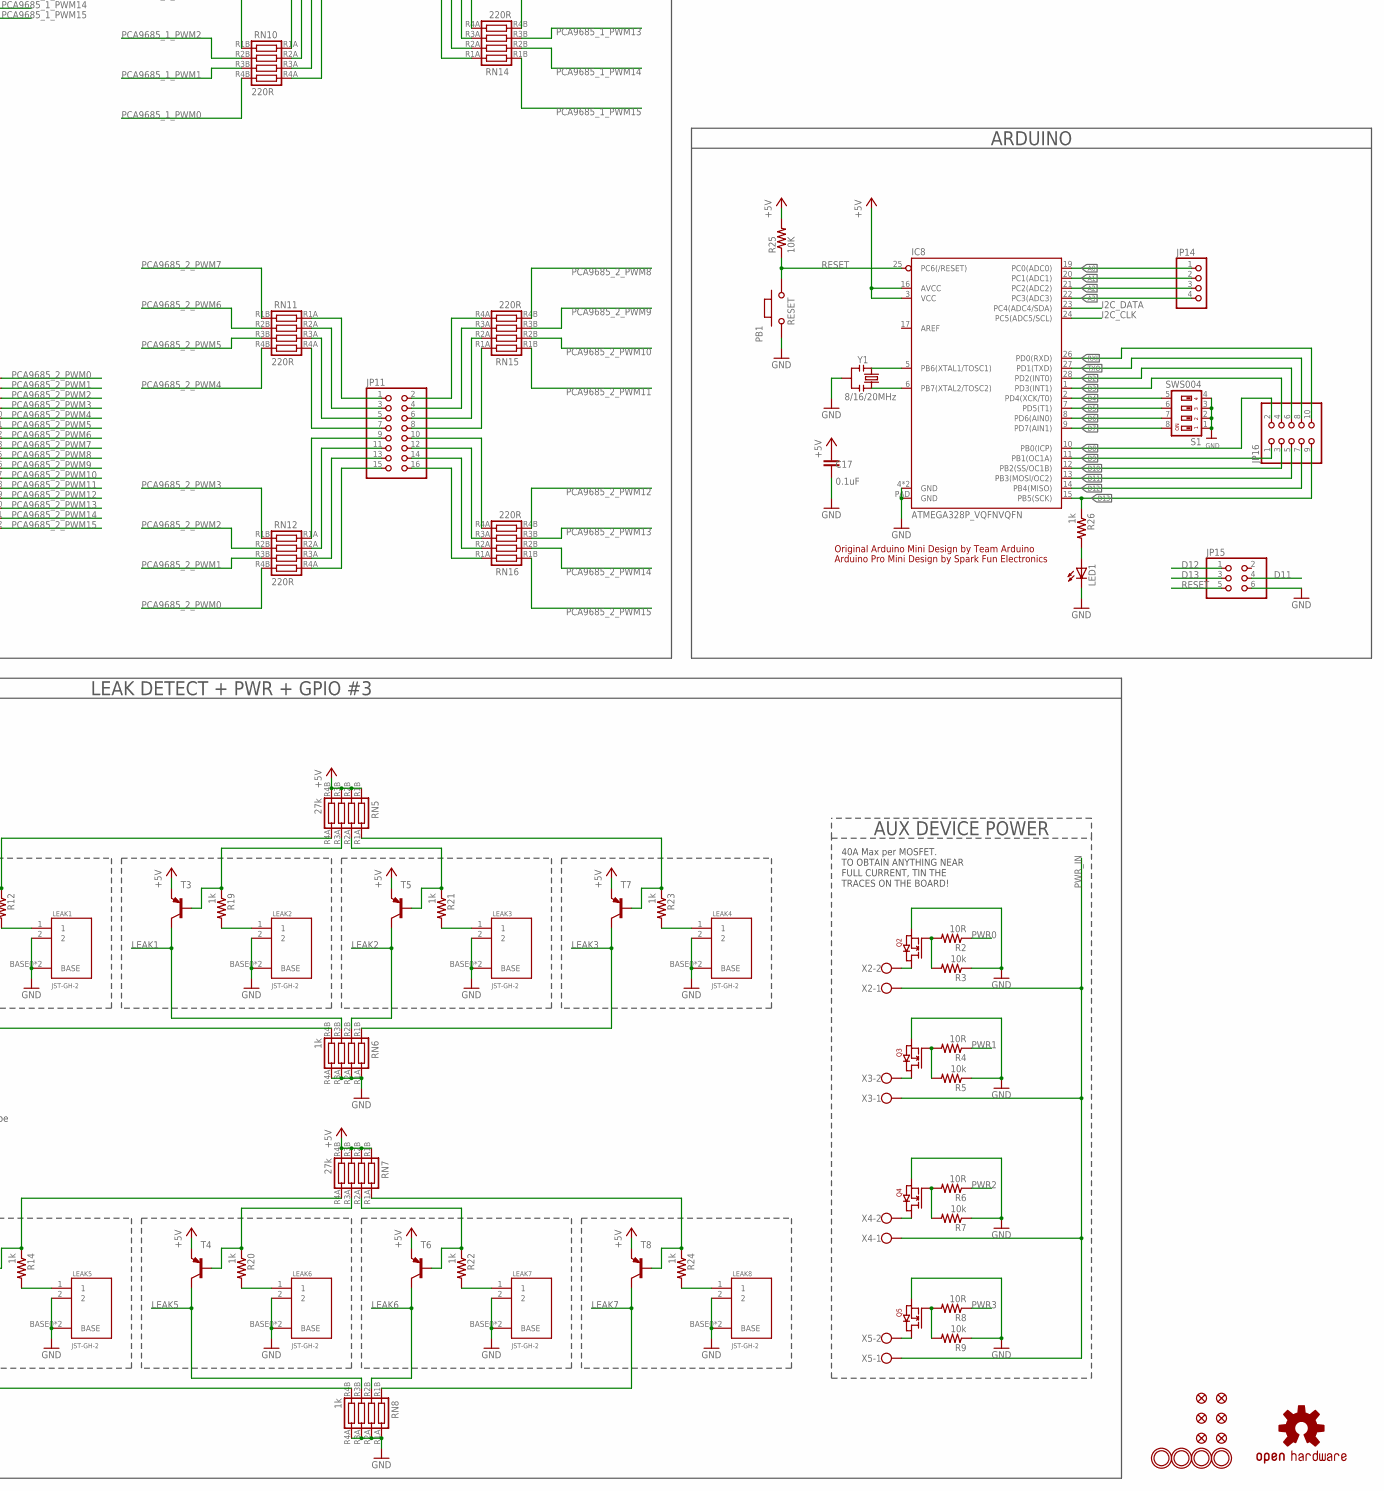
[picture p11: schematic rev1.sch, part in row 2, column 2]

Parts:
1, 2, 3, 4: MOUNTINGHOLE2.5; MOUNTINGHOLE_2.5_PLATED
5: OSHW-LOGOS; OSHW-LOGO-S
C1, C2: 100uF; 153CLV-0807
C3, C4, C5, C8, C14: 1uF; 0805-NO
C6, C7: 1nF; 0805-NO
C9, C10: .1uF; 0805-NO
C11, C12, C13, C15, C16: 10uF; 0805-NO
C17: 0.1uF; C0805
D1: BZX84B3V0-7-F; SOT23
F1, F3: 3A; 2920_(7351_METRIC)
F2: 0.5A; 1210_(3225METRIC)
FID1, FID2, FID3, FID4, FID5, FID6: FIDUCIAL""; FIDUCIAL_1MM
IC1, IC2, IC3: U2; MCP3008
IC4, IC5, IC9: MCP23017ML; QFN28-ML_6X6MM
IC6, IC7: PCA9685; TSSOP28
IC8: ATMEGA328P_VQFNVQFN; VQFN-28
IC10: LM62C; SOT23-R
IC11: MS563702BA03-50; MS5637
IC12, IC13: ACS780LLRTR-050U-T; ACS781
JMP1, JMP2, JMP3, JMP4, JMP5, JMP6, JMP7, JMP8, JMP9, JMP10, JMP11, JMP12, JMP13, JMP14, JMP15, JMP16, JMP17, JMP18, JMP19, JMP20, JMP21, JMP22, JMP23: 0R-JUMPC; C0R-JMP
JP1, JP2: PINHD-1X2; 1X02
JP3, JP5, JP14: PINHD-1X4; 1X04
JP4: PINHD-1X3; 1X03
JP6: PINHD-2X20; 2X20
JP7, JP9: PINHD-1X1; 1X01
JP8, JP10, JP11, JP12, JP13: PINHD-2X8; 2X08
JP15: PINHD-2X3; 2X03
JP16: PINHD-2X5; 2X05
LEAK1, LEAK2, LEAK3, LEAK4, LEAK5, LEAK6, LEAK7, LEAK8: JST-GH-2; JST-GH
LED1, LED2, LED3, LED4: LED_E; LED_1206
PB1: RESET; SMD_157SW
Q1: 1212_PFET; POWERPACK_1212-8
Q2, Q3, Q4, Q5: 1212_NFET; POWERPACK_1212-8
R1, R10, R11: 10k; R0402
R2, R4, R6, R8: 10R; R0805
R3, R5, R7, R9: 10k; R0805
R12, R13, R14, R15, R19, R20, R21, R22, R23, R24: 1k; R0402
R16: 11k; R0402
R17: 2.2k; R0402
R18: 400R; R0402
R25: 10K; R0805
R26, R27, R28, R29: 1k; R0805
RN1, RN2, RN3, RN4: 10k; 0804_RN
RN5, RN7: 27k; 0804_RN
RN6, RN8: 1k; 0804_RN
RN9, RN10, RN11, RN12, RN13, RN14, RN15, RN16: 220R; 0804_RN
S1: SWS004; SMS-004
T1: MMBT3906; SOT23-BEC
T2, T3, T4, T5, T6, T7, T8: BC807-40-PNP-SOT23-BEC; SOT23-BEC
TP5, TP6, TP7: PTR1TP06R; TP06R
X1, X2, X3, X4, X5, X6, X7: W237-102
Y1: 8/16/20MHz; RESONATOR-SMD-1:1

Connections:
1-WIRE: JP6.7, JP7.1
3V_REF: D1.3 (C), IC1.CH2, R18.2
+3V3: C9.1, C10.1, F2.1, IC1.CH4, IC12.1 (VCC), IC13.1 (VCC)
+5V: C1.+, C3.1, C4.1, C5.1, C8.1, C11.1, C12.1, C13.1, C14.1, C15.1, C16.1, C17.2, F1.2, IC1.CH5, IC1.VDD, IC1.VREF, IC2.VDD, IC2.VREF, IC3.VDD, IC3.VREF, IC4.5 (VDD), IC4.14 (!RESET), IC5.5 (VDD), IC5.14 (!RESET), IC6.28 (VDD), IC7.28 (VDD), IC8.3 (VCC), IC8.16 (AVCC), IC9.5 (VDD), IC9.14 (!RESET), IC10.1 (VCC), IC11.VDD, JMP3.3, JMP4.3, JMP5.3, JMP6.3, JMP7.3, JMP8.3, JMP9.3, JMP10.3, JMP11.3, JMP12.3, JMP13.3, JMP14.3, JMP15.1, JMP16.1, JMP17.1, JMP18.1, JMP19.1, JMP20.1, JMP21.1, JMP22.1, JMP23.1, JP6.2, JP6.4, R18.1, R25.2, R27.2, RN5.R1B (1), RN5.R2B (2), RN5.R3B (3), RN5.R4B (4), RN7.R1B (1), RN7.R2B (2), RN7.R3B (3), RN7.R4B (4), T1.E, T2.E, T3.E, T4.E, T5.E, T6.E, T7.E, T8.E
+12V: C2.+, F3.2, JP3.4, R17.2, R28.2
A0: IC8.19 (PC0(ADC0)), JP14.1
A1: IC8.20 (PC1(ADC1)), JP14.2
A2: IC8.21 (PC2(ADC2)), JP14.3
A3: IC8.22 (PC3(ADC3)), JP14.4
ADC0_1: IC3.CH0, JP8.2
ADC0_2: IC2.CH0, JP8.9
ADC3_1: IC3.CH3, JP8.8
ADC3_2: IC2.CH3, JP8.15
ADC4_1: IC3.CH4, JP8.1
ADC4_2: IC2.CH4, JP8.10
ADC7_1: IC3.CH7, JP8.7
ADC7_2: IC2.CH7, JP8.16
CS_ANALOG1: IC3.CS (/CS), JMP2.2
CS_ANALOG2: IC2.CS (/CS), JMP1.2, JMP1.3
CS_ANALOG3: IC1.CS (/CS), JP6.32
CURR_SNS_0: C6.1, IC1.CH1, R10.2
CURR_SNS_1: C7.1, IC1.CH0, R11.2
D2: IC8.28 (PD2(INT0)), JP16.6
D3: IC8.1 (PD3(INT1)), JP16.4
D4: IC8.2 (PD4(XCK/T0)), S1.5
D5: IC8.7 (PD5(T1)), S1.6
D6: IC8.8 (PD6(AIN0)), S1.7
D7: IC8.9 (PD7(AIN1)), S1.8
D8: IC8.10 (PB0(ICP)), JP16.2
D9: IC8.11 (PB1(OC1A)), JP16.1
D10: IC8.12 (PB2(SS/OC1B)), JP16.3
D11: IC8.13 (PB3(MOSI/OC2)), JP15.4, JP16.5
D12: IC8.14 (PB4(MISO)), JP15.1, JP16.7
D13: IC8.15 (PB5(SCK)), JP15.3, JP16.9, R26.1
GND: C1.-, C2.-, C3.2, C4.2, C5.2, C6.2, C7.2, C8.2, C9.2, C10.2, C11.2, C12.2, C13.2, C14.2, C15.2, C16.2, C17.1, D1.1 (A), IC1.AGND, IC1.DGND (GND), IC2.AGND, IC2.DGND (GND), IC3.AGND, IC3.DGND (GND), IC4.6 (VSS), IC5.6 (VSS), IC6.14 (GND), IC6.25 (EXTCLK), IC7.14 (GND), IC7.25 (EXTCLK), IC8.4 (GND), IC8.18 (GND), IC8.PAD (GND), IC9.6 (VSS), IC9.EXP (VSS), IC10.3 (GND), IC11.GND, IC12.2 (GND), IC12.4 (GND), IC12.7 (GND), IC13.2 (GND), IC13.4 (GND), IC13.7 (GND), JMP15.3, JMP16.3, JMP17.3, JMP18.3, JMP19.3, JMP20.3, JMP21.3, JMP22.3, JMP23.3, JP3.1, JP3.2, JP6.6, JP6.9, JP6.14, JP6.20, JP6.25, JP6.30, JP6.34, JP6.39, JP15.6, LEAK1.2, LEAK1.BASE0 (BASE), LEAK1.BASE1 (BASE), LEAK2.2, LEAK2.BASE0 (BASE), LEAK2.BASE1 (BASE), LEAK3.2, LEAK3.BASE0 (BASE), LEAK3.BASE1 (BASE), LEAK4.2, LEAK4.BASE0 (BASE), LEAK4.BASE1 (BASE), LEAK5.2, LEAK5.BASE0 (BASE), LEAK5.BASE1 (BASE), LEAK6.2, LEAK6.BASE0 (BASE), LEAK6.BASE1 (BASE), LEAK7.2, LEAK7.BASE0 (BASE), LEAK7.BASE1 (BASE), LEAK8.2, LEAK8.BASE0 (BASE), LEAK8.BASE1 (BASE), LED1.C, LED2.C, LED3.C, LED4.C, PB1.1, Q2.S1 (SOURCE), Q2.S2 (SOURCE), Q2.S3 (SOURCE), Q3.S1 (SOURCE), Q3.S2 (SOURCE), Q3.S3 (SOURCE), Q4.S1 (SOURCE), Q4.S2 (SOURCE), Q4.S3 (SOURCE), Q5.S1 (SOURCE), Q5.S2 (SOURCE), Q5.S3 (SOURCE), R1.2, R3.1, R5.1, R7.1, R9.1, R13.1, R15.1, RN1.R1B (1), RN1.R2B (2), RN1.R3B (3), RN1.R4B (4), RN2.R1B (1), RN2.R2B (2), RN2.R3B (3), RN2.R4B (4), RN3.R1B (1), RN3.R2B (2), RN3.R3B (3), RN3.R4B (4), RN4.R1B (1), RN4.R2B (2), RN4.R3B (3), RN4.R4B (4), RN6.R1A (1A), RN6.R2A (2A), RN6.R3A (3A), RN6.R4A (4A), RN8.R1A (1A), RN8.R2A (2A), RN8.R3A (3A), RN8.R4A (4A), S1.1, S1.2, S1.3, S1.4, X1.2, Y1.2
GPA0_1: IC4.17 (GPA0), JP12.16
GPA0_2: IC5.17 (GPA0), JP13.16
GPA7_1: IC4.24 (GPA7), JP12.2
GPA7_2: IC5.24 (GPA7), JP13.2
GPB0_1: IC4.25 (GPB0), JP12.1
GPB0_2: IC5.25 (GPB0), JP13.1
GPB4_3: IC9.1 (GPB4), TP5.TP
GPB5_3: IC9.2 (GPB5), TP6.TP
GPB6_3: IC9.3 (GPB6), TP7.TP
GPB7_1: IC4.4 (GPB7), JP12.15
GPB7_2: IC5.4 (GPB7), JP13.15
I2C_CLK: IC4.8 (SCL), IC5.8 (SCL), IC6.26 (SCL), IC7.26 (SCL), IC8.24 (PC5(ADC5/SCL)), IC9.8 (SCL), IC11.SCL, JP1.2, JP6.5
I2C_DATA: IC4.9 (SDA), IC5.9 (SDA), IC6.27 (SDA), IC7.27 (SDA), IC8.23 (PC4(ADC4/SDA)), IC9.9 (SDA), IC11.SDA, JP1.1, JP6.3
LEAK0: IC9.17 (GPA0), RN6.R4B (4), T1.C
LEAK1: IC9.18 (GPA1), RN6.R3B (3), T3.C
LEAK2: IC9.19 (GPA2), RN6.R2B (2), T5.C
LEAK3: IC9.20 (GPA3), RN6.R1B (1), T7.C
LEAK4: IC9.21 (GPA4), RN8.R4B (4), T2.C
LEAK5: IC9.22 (GPA5), RN8.R3B (3), T4.C
LEAK6: IC9.23 (GPA6), RN8.R2B (2), T6.C
LEAK7: IC9.24 (GPA7), RN8.R1B (1), T8.C
LEAK_WARN: IC9.4 (GPB7), R29.2
MCP1_GPA1: IC4.18 (GPA1), JP12.14
MCP1_GPA2: IC4.19 (GPA2), JP12.12
MCP1_GPA7: IC4.23 (GPA6), JP12.4
MCP23017_1_A0: IC4.11 (A0), JMP17.2
MCP23017_1_A1: IC4.12 (A1), JMP15.2
MCP23017_1_A2: IC4.13 (A2), JMP18.2
MCP23017_2_A0: IC5.11 (A0), JMP19.2
MCP23017_2_A1: IC5.12 (A1), JMP16.2
MCP23017_2_A2: IC5.13 (A2), JMP20.2
MCP23017_3_A0: IC9.11 (A0), JMP22.2
MCP23017_3_A1: IC9.12 (A1), JMP21.2
MCP23017_3_A2: IC9.13 (A2), JMP23.2
unnamed: Q2.G (GATE), R2.2, R3.2
unnamed: JP11.14, RN16.R2A (2A)
unnamed: Q1.G (GATE), R1.1
unnamed: LED2.A, R27.1
unnamed: LEAK1.1, R12.2
unnamed: LEAK2.1, R19.2
unnamed: LED3.A, R28.1
unnamed: IC2.CH6, JP8.14
unnamed: LED1.A, R26.2
unnamed: IC2.CH5, JP8.12
unnamed: IC1.CH6, R15.2, R17.1
unnamed: IC8.6 (PB7(XTAL2/TOSC2)), Y1.3
unnamed: R21.1, RN5.R2A (2A), T5.B
unnamed: IC8.5 (PB6(XTAL1/TOSC1)), Y1.1
unnamed: F3.1, Q1.S1 (SOURCE), Q1.S2 (SOURCE), Q1.S3 (SOURCE)
unnamed: LEAK3.1, R21.2
unnamed: LED4.A, R29.1
unnamed: IC3.CH6, JP8.5
unnamed: IC3.CH5, JP8.3
unnamed: JP11.11, RN12.R2A (2A)
unnamed: JP10.7, RN9.R4A (4A)
unnamed: JP10.9, RN10.R1A (1A)
unnamed: JP10.11, RN10.R2A (2A)
unnamed: JP10.13, RN10.R3A (3A)
unnamed: JP10.15, RN10.R4A (4A)
unnamed: JP10.5, RN9.R3A (3A)
unnamed: JP10.3, RN9.R2A (2A)
unnamed: JP10.1, RN9.R1A (1A)
unnamed: JP10.10, RN14.R4A (4A)
unnamed: JP10.12, RN14.R3A (3A)
unnamed: JP10.14, RN14.R2A (2A)
unnamed: JP10.16, RN14.R1A (1A)
unnamed: JP10.8, RN13.R1A (1A)
unnamed: JP10.6, RN13.R2A (2A)
unnamed: JP10.4, RN13.R3A (3A)
unnamed: JP10.2, RN13.R4A (4A)
unnamed: JP11.13, RN12.R3A (3A)
unnamed: JP11.15, RN12.R4A (4A)
unnamed: JP11.7, RN11.R4A (4A)
unnamed: JP11.9, RN12.R1A (1A)
unnamed: JP11.5, RN11.R3A (3A)
unnamed: JP11.3, RN11.R2A (2A)
unnamed: JP11.1, RN11.R1A (1A)
unnamed: JP11.2, RN15.R4A (4A)
unnamed: JP11.4, RN15.R3A (3A)
unnamed: JP11.6, RN15.R2A (2A)
unnamed: JP11.10, RN16.R4A (4A)
unnamed: JP11.8, RN15.R1A (1A)
unnamed: JP11.12, RN16.R3A (3A)
unnamed: Q2.D0 (DRAIN), Q2.D1 (DRAIN), Q2.D2 (DRAIN), Q2.D3 (DRAIN), Q2.D4 (DRAIN), X2.2
unnamed: JP11.16, RN16.R1A (1A)
unnamed: Q3.G (GATE), R4.2, R5.2
unnamed: Q3.D0 (DRAIN), Q3.D1 (DRAIN), Q3.D2 (DRAIN), Q3.D3 (DRAIN), Q3.D4 (DRAIN), X3.2
unnamed: Q4.D0 (DRAIN), Q4.D1 (DRAIN), Q4.D2 (DRAIN), Q4.D3 (DRAIN), Q4.D4 (DRAIN), X4.2
unnamed: Q4.G (GATE), R6.2, R7.2
unnamed: Q5.D0 (DRAIN), Q5.D1 (DRAIN), Q5.D2 (DRAIN), Q5.D3 (DRAIN), Q5.D4 (DRAIN), X5.2
unnamed: IC13.6 (IP-), X7.1
unnamed: F1.1, JP3.3
unnamed: IC3.CH2, JP8.6
unnamed: IC3.CH1, JP8.4
unnamed: F2.2, JP6.1
unnamed: IC2.CH2, JP8.13
unnamed: IC2.CH1, JP8.11
unnamed: R12.1, RN5.R4A (4A), T1.B
unnamed: R14.1, RN7.R4A (4A), T2.B
unnamed: IC5.26 (GPB1), JP13.3
unnamed: IC5.27 (GPB2), JP13.5
unnamed: R19.1, RN5.R3A (3A), T3.B
unnamed: IC5.28 (GPB3), JP13.7
unnamed: IC5.1 (GPB4), JP13.9
unnamed: IC5.2 (GPB5), JP13.11
unnamed: Q5.G (GATE), R8.2, R9.2
unnamed: LEAK4.1, R23.2
unnamed: R23.1, RN5.R1A (1A), T7.B
unnamed: LEAK5.1, R14.2
unnamed: LEAK6.1, R20.2
unnamed: R20.1, RN7.R3A (3A), T4.B
unnamed: IC5.3 (GPB6), JP13.13
unnamed: IC12.5 (IP+), X6.2
unnamed: IC12.6 (IP-), X6.1
unnamed: IC5.23 (GPA6), JP13.4
unnamed: IC5.22 (GPA5), JP13.6
unnamed: IC5.21 (GPA4), JP13.8
unnamed: IC5.20 (GPA3), JP13.10
unnamed: IC5.19 (GPA2), JP13.12
unnamed: IC5.18 (GPA1), JP13.14
unnamed: IC13.5 (IP+), X7.2
unnamed: IC13.3 (VOUT), R11.1
unnamed: IC4.26 (GPB1), JP12.3
unnamed: IC4.27 (GPB2), JP12.5
unnamed: IC4.28 (GPB3), JP12.7
unnamed: IC4.1 (GPB4), JP12.9
unnamed: IC4.2 (GPB5), JP12.11
unnamed: IC4.3 (GPB6), JP12.13
unnamed: LEAK7.1, R22.2
unnamed: IC12.3 (VOUT), R10.1
unnamed: R22.1, RN7.R2A (2A), T6.B
unnamed: IC4.22 (GPA5), JP12.6
unnamed: IC4.21 (GPA4), JP12.8
unnamed: IC4.20 (GPA3), JP12.10
unnamed: LEAK8.1, R24.2
unnamed: R24.1, RN7.R1A (1A), T8.B
OLED_RST: JP6.27
PCA9685_1_A0: IC6.1 (A0), JMP3.1, JMP3.2, RN3.R2A (2A)
PCA9685_1_A1: IC6.2 (A1), JMP4.1, JMP4.2, RN3.R1A (1A)
PCA9685_1_A2: IC6.3 (A2), JMP5.1, JMP5.2, RN1.R4A (4A)
PCA9685_1_A3: IC6.4 (A3), JMP6.1, JMP6.2, RN1.R3A (3A)
PCA9685_1_A4: IC6.5 (A4), JMP7.1, JMP7.2, RN1.R2A (2A)
PCA9685_1_A5: IC6.24 (A5), JMP8.1, JMP8.2, RN1.R1A (1A)
PCA9685_1_PWM0: IC6.6 (PWM0), RN10.R4B (4)
PCA9685_1_PWM1: IC6.7 (PWM1), RN10.R3B (3)
PCA9685_1_PWM2: IC6.8 (PWM2), RN10.R2B (2)
PCA9685_1_PWM3: IC6.9 (PWM3), RN10.R1B (1)
PCA9685_1_PWM4: IC6.10 (PWM4), RN9.R4B (4)
PCA9685_1_PWM5: IC6.11 (PWM5), RN9.R3B (3)
PCA9685_1_PWM6: IC6.12 (PWM6), RN9.R2B (2)
PCA9685_1_PWM7: IC6.13 (PWM7), RN9.R1B (1)
PCA9685_1_PWM8: IC6.15 (PWM8), RN13.R4B (4)
PCA9685_1_PWM9: IC6.16 (PWM9), RN13.R3B (3)
PCA9685_1_PWM10: IC6.17 (PWM10), RN13.R2B (2)
PCA9685_1_PWM11: IC6.18 (PWM11), RN13.R1B (1)
PCA9685_1_PWM12: IC6.19 (PWM12), RN14.R4B (4)
PCA9685_1_PWM13: IC6.20 (PWM13), RN14.R3B (3)
PCA9685_1_PWM14: IC6.21 (PWM14), RN14.R2B (2)
PCA9685_1_PWM15: IC6.22 (PWM15), RN14.R1B (1)
PCA9685_2_A0: IC7.1 (A0), JMP9.1, JMP9.2, RN4.R2A (2A)
PCA9685_2_A1: IC7.2 (A1), JMP10.1, JMP10.2, RN4.R1A (1A)
PCA9685_2_A2: IC7.3 (A2), JMP11.1, JMP11.2, RN2.R4A (4A)
PCA9685_2_A3: IC7.4 (A3), JMP12.1, JMP12.2, RN2.R3A (3A)
PCA9685_2_A4: IC7.5 (A4), JMP13.1, JMP13.2, RN2.R2A (2A)
PCA9685_2_A5: IC7.24 (A5), JMP14.1, JMP14.2, RN2.R1A (1A)
PCA9685_2_PWM0: IC7.6 (PWM0), RN12.R4B (4)
PCA9685_2_PWM1: IC7.7 (PWM1), RN12.R3B (3)
PCA9685_2_PWM2: IC7.8 (PWM2), RN12.R2B (2)
PCA9685_2_PWM3: IC7.9 (PWM3), RN12.R1B (1)
PCA9685_2_PWM4: IC7.10 (PWM4), RN11.R4B (4)
PCA9685_2_PWM5: IC7.11 (PWM5), RN11.R3B (3)
PCA9685_2_PWM6: IC7.12 (PWM6), RN11.R2B (2)
PCA9685_2_PWM7: IC7.13 (PWM7), RN11.R1B (1)
PCA9685_2_PWM8: IC7.15 (PWM8), RN15.R4B (4)
PCA9685_2_PWM9: IC7.16 (PWM9), RN15.R3B (3)
PCA9685_2_PWM10: IC7.17 (PWM10), RN15.R2B (2)
PCA9685_2_PWM11: IC7.18 (PWM11), RN15.R1B (1)
PCA9685_2_PWM12: IC7.19 (PWM12), RN16.R4B (4)
PCA9685_2_PWM13: IC7.20 (PWM13), RN16.R3B (3)
PCA9685_2_PWM14: IC7.21 (PWM14), RN16.R2B (2)
PCA9685_2_PWM15: IC7.22 (PWM15), RN16.R1B (1)
PCA9685_OE: IC6.23 (#OE), IC7.23 (#OE), JP6.28, RN3.R3A (3A), RN4.R3A (3A)
PWR0: IC9.25 (GPB0), R2.1
PWR1: IC9.26 (GPB1), R4.1
PWR2: IC9.27 (GPB2), R6.1
PWR3: IC9.28 (GPB3), R8.1
PWR_IN: Q1.D0 (DRAIN), Q1.D1 (DRAIN), Q1.D2 (DRAIN), Q1.D3 (DRAIN), Q1.D4 (DRAIN), X1.1, X2.1, X3.1, X4.1, X5.1
RESET: IC8.25 (PC6(/RESET)), JP15.5, PB1.2, R25.1
RXI: IC8.26 (PD0(RXD)), JP16.10
SPI_CE0: JMP2.1, JP6.24
SPI_CE1: JMP1.1, JP6.26
SPI_CLK: IC1.CLK, IC2.CLK, IC3.CLK, JP4.1, JP6.23
SPI_CS_1: JP5.4, JP6.12
SPI_CS_2: JP5.3, JP6.16
SPI_CS_3: JP5.2, JP6.18
SPI_CS_4: JP5.1, JP6.22
SPI_MISO: IC1.DOUT, IC2.DOUT, IC3.DOUT, JP4.3, JP6.21
SPI_MOSI: IC1.DIN, IC2.DIN, IC3.DIN, JP4.2, JP6.19
TEMP_AMB: IC1.CH3, IC10.2 (VOUT)
TXO: IC8.27 (PD1(TXD)), JP16.8
UART_RXD: JP2.1, JP6.10
UART_TXD: JP2.2, JP6.8
VBAT_ADC: IC1.CH7, R13.2, R16.1
VCC: JP9.1, R16.2

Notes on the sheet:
+12V WILL NOT be at the same potential as PWR_IN due to voltage drop in Q1 and the fuse.
REVERSE POLARITY PROTECTION
AUX DEVICE POWER
VIN MGMT
LED INDICATORS
Voltage Measurement Typically: +48V (ROV Tether voltage. 55V tolerant) +12V (Motors/internal wiring. 55V tolerant) +5V (5V Tolerant) +3V3 (5V Tolerant)
I2C Address = 0x1,A5,A4,A3,A2,A1,A1,RW
Open = 0 / Closed = 1 'Open' choice marked with a dot on the board.
40A Max per MOSFET. TO OBTAIN ANYTHING NEAR FULL CURRENT, TIN THE TRACES ON THE BOARD!
Q1 Max current = 35A
ADC/ANALOG SENSORS
POWER LINE MEASUREMENT
+5V BUCK REGULATOR
CONNECTION HEADERS + 8 DIP SWITCH
PWM CONTROLLERS
ADDRESS SELECTION
Use 12V 3A+ Supply
GPIO CONTROLLERS
3V Zener Voltage Refrence
DIGITAL SENSORS
AMBIENT PRESSURE
V. REF
AMBIENT TEMP
CURRENT
8 CHANNEL 10 BIT ADC x2
Original Arduino Mini Design by Team Arduino
Arduino Pro Mini Design by Spark Fun Electronics
LEAK DETECT + PWR + GPIO #3
ARDUINO
Emergency Telemetry: These should be used for important signals which need to be constantly monitored.

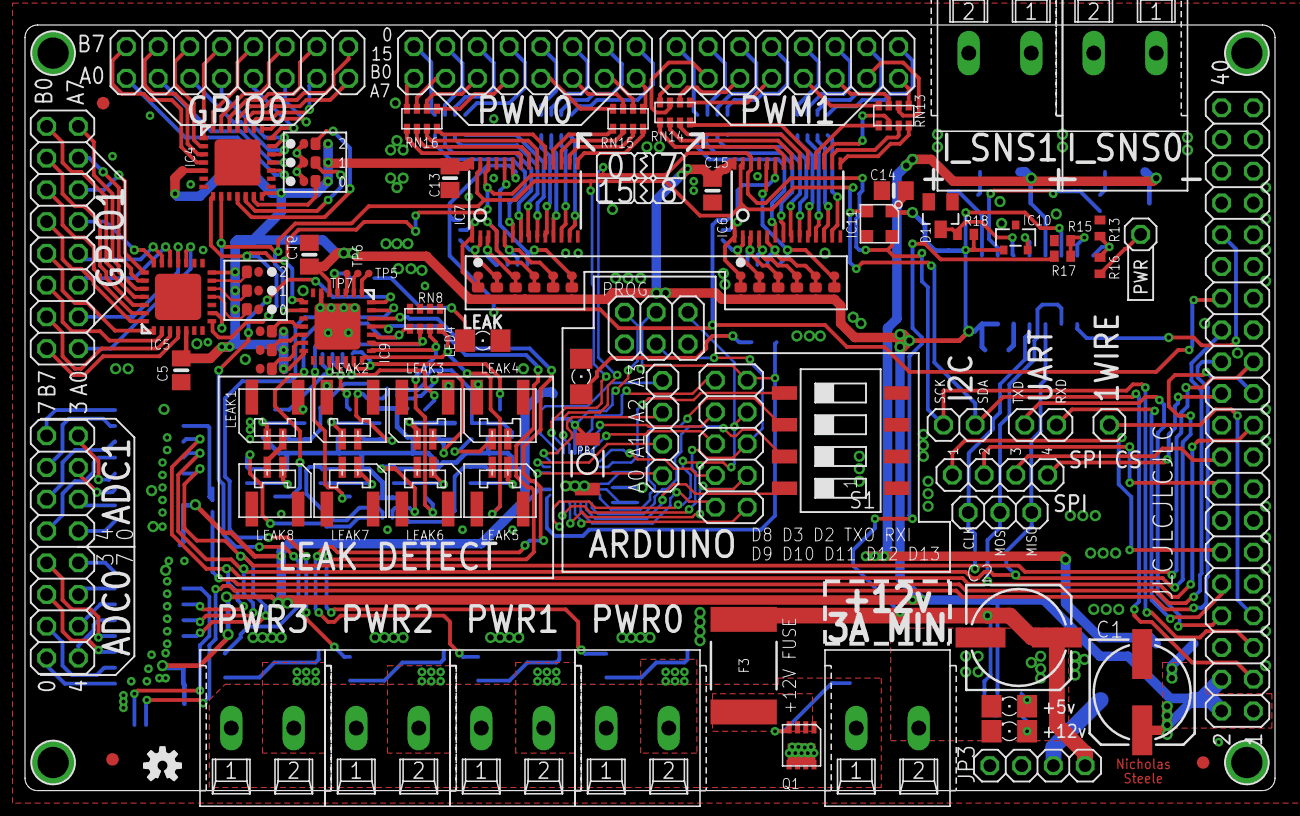
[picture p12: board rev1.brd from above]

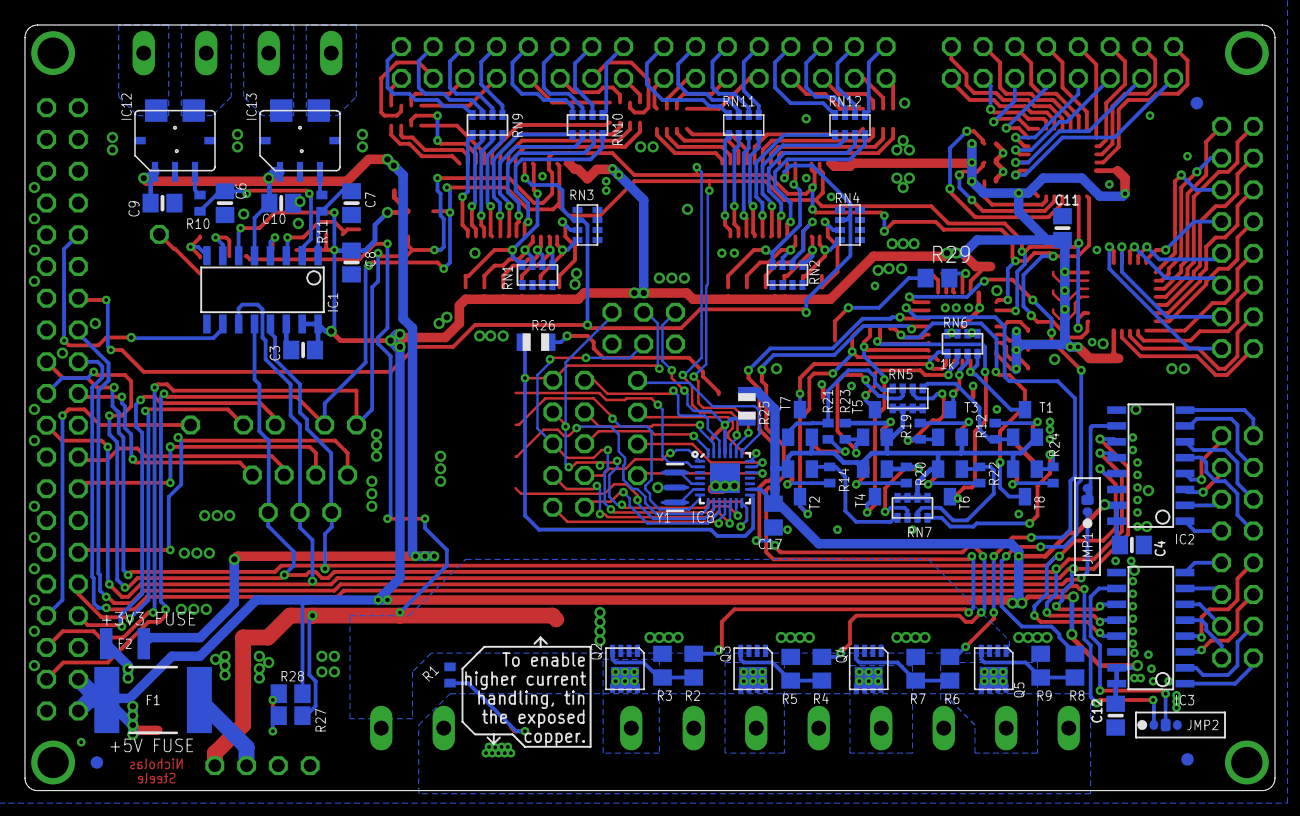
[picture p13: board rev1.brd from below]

Board: 2 copper layers, 100.0 x 61.2 mm, 167 parts (71 on the bottom side), 238 nets.

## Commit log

2020-07-25 Initial commit - schematic and board.
2020-07-25 Initial commit - eagle files.
    [rev1.brd, rev1.sch]
2020-08-25 Add BOM
    [rev1-bom.xlsx]
2020-10-23 Add cream file
    [rev1-bcream.dxf, rev1-tcream.dxf]

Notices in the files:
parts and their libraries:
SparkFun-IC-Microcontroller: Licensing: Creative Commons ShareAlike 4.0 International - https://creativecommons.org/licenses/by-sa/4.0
